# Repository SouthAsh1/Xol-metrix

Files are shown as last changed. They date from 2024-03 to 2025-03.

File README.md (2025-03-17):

# Xol-metrix

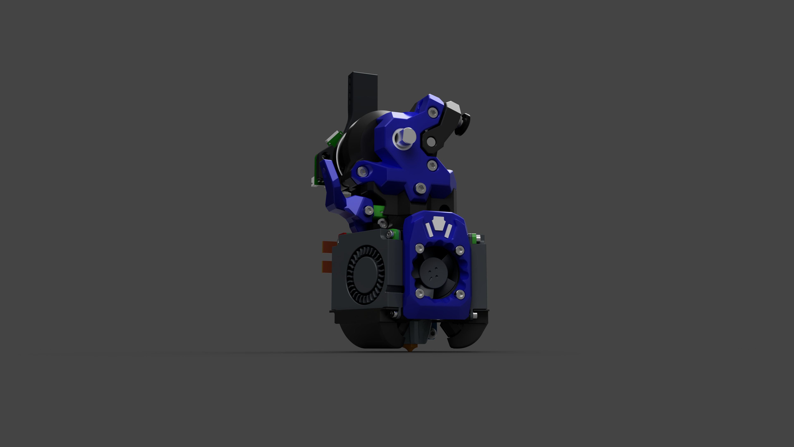
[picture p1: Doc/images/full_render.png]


This is a filament cutter designed around the Xol Toolhead platform thanks to everyone that helped with the BETA process to get this project into a phase that I am comfortable in calling a released state. There will still be some small adjustments I will make when more feedback is given.

Now supports current version of Xol Toolhead! CAD included.

Does support non-heatset version of Xol, however, the cutting arm mount still requires it. So anything that is non-heatset does not require heatsets asside from that.

I do ask that if anyone makes any mods let me know so we can discuss if it makes since to put it in the repo.

So far the project supports the following.

### Hotends

- Dragon SF/UHF/ACE
- NF-Crazy
- Rapido SF/UHF
- Rapido V2 SF/UHF
- Revo Voron
- DropEffect XG
- Bambu Labs

### Extruders

- [Wrist Watch G2](https://github.com/tetsu97/WristWatch-G2-Extruder)
- [Sherpa Mini](https://github.com/Annex-Engineering/Sherpa_Mini-Extruder)
- [Orbiter](https://www.orbiterprojects.com/orbiter-v2-0/)
- [G2SA](https://github.com/tetsu97/Galileo2)
- [VZ Hextrudort](https://github.com/VzBoT3D/Vz-HextrudORT) / [Bondtech LGX Lite](https://www.bondtech.se/product/lgx-lite-v2-large-gears-extruder/)
## BOM

This is addition to your choice of Xol Toolhead build BOM

|Qty|Item|Notes|
|-|-|-|
|2|M2 Flanged Heatset Insert|Specifically this heatset [HM20X157C](https://www.digikey.com/en/products/detail/tri-star-industries-inc/HM20X157C/14205393)|
|1|M2.5 Heatset Insert|3.5mm Outer Diameter x 4mm Length `Same as Xol Toolhead BOM`|
|3|M2 Heatset Insert|3.5mm Outer Diameter x 4mm Length `Same as Xol Toolhead BOM`|
|2|M2.5x15 SHCS|For mounting the arm to the frame and blade holder.|
|3|M2x8 SHCS|To hold the extruder adapter together.|
|1|5.5mm Ball Bearing|For toolhead filament sensor. `Same as ERCF BOM`|
|1|Omron D2F Micro Switch|Tis be switch that does clicky things.|
|2|M2x10 Self Tapping|It really doesn't matter what type just has to self tap.|
|1|0.5x4x15 Spring|Any spring that is 4mm in diameter and no longer than 15mm should work your milage may vary for cutting force needed.|
|Yes|PTFE Tube|Still working out exact lengths and possibly cutting jigs.|
|**OPTIONS**|
|1|#4 metal hobby blades|Same blade used in the Filametrix only cut to a different length.|
|**OR**|
|1|OLFA KB4-F/5|Different blade otion if you are having problems with #4 blades.|
|**OPTIONAL**|
|1|M3 Grubscrew|Same ones used to secure pulleys **totally optional**.|

## Acknowledgements

 - [Xol-Toolhead](https://github.com/Armchair-Heavy-Industries/Xol-Toolhead) For Xol Toolhead project
 - [WristWatch-G2-Extruder](https://github.com/tetsu97/WristWatch-G2-Extruder) For WWG2 and Extruder adapter
 - [Filametrix](https://github.com/sorted01/Filametrix) For the orginal mod idea
 - Thanks to Tea/`nurse.shark` for alowing me to use the Xolametrix name (I did change it slightly)
 - Thanks to scheini79/`zerodegree79` for the XolPAP modification.

## Feedback

- [Armchair Discord User Projects Discussion](https://discord.com/channels/1029426383614648421/1195580104659710053)
- My Discord `southash1`

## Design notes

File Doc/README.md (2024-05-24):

# Xol-metrix Assembly

This project assumes you know how to build the standard Xol Toolhead with this build assembly thrown into the mix.

|	Notes	|	Image	|
|	---	|	---	|
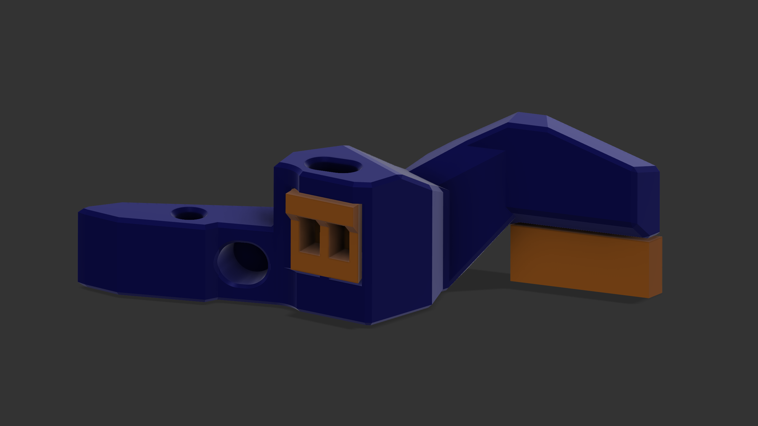
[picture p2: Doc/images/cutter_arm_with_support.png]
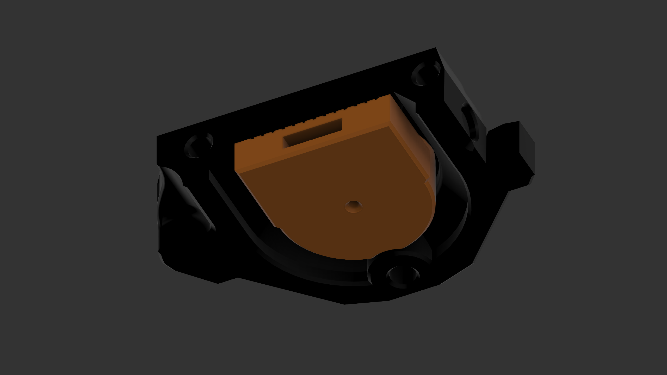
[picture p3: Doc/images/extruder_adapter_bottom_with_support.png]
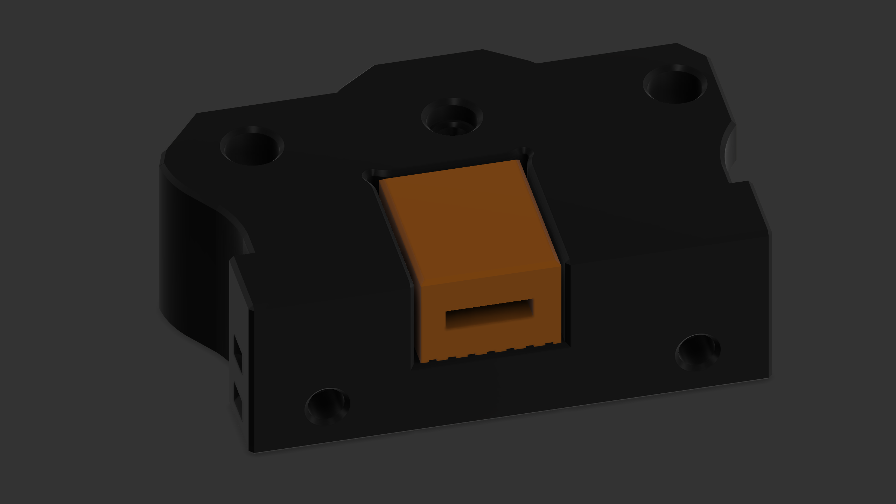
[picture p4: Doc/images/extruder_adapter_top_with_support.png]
|Remove the support material in orange. They should break away with ease.|	|
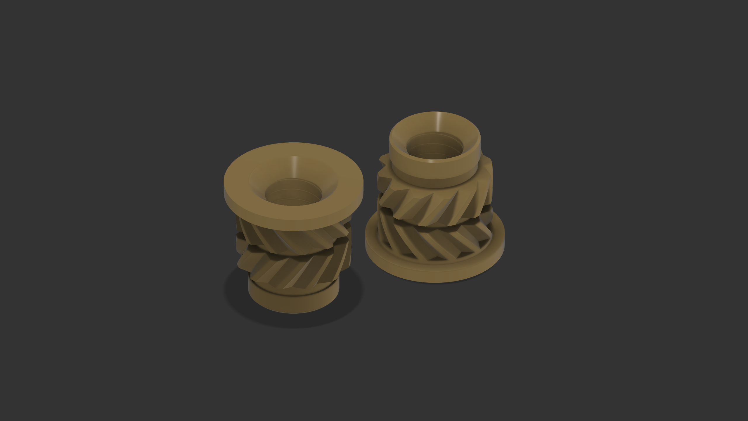
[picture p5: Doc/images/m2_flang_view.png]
|Next drill out the 2 `Flanged M2` Heatset Inserts with a `5/64 inch drill bit`. Then use the `#2 center drill bit` to chamfer the top of one and the bottom of the other. ⚠⚠ **Make sure you thuroghly clean the inserts of brass when done!** ⚠⚠||
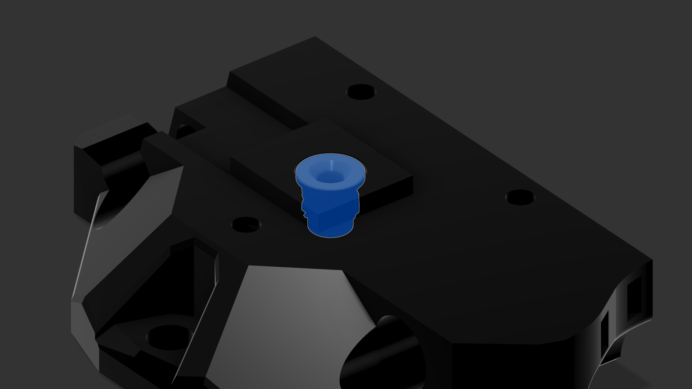
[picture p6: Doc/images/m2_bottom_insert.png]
|Insert the `Flanged M2` heatset with the **top chamfer** into the `extruder_adapter_bottom.stl` with the flang surface flush with the printed surface.||
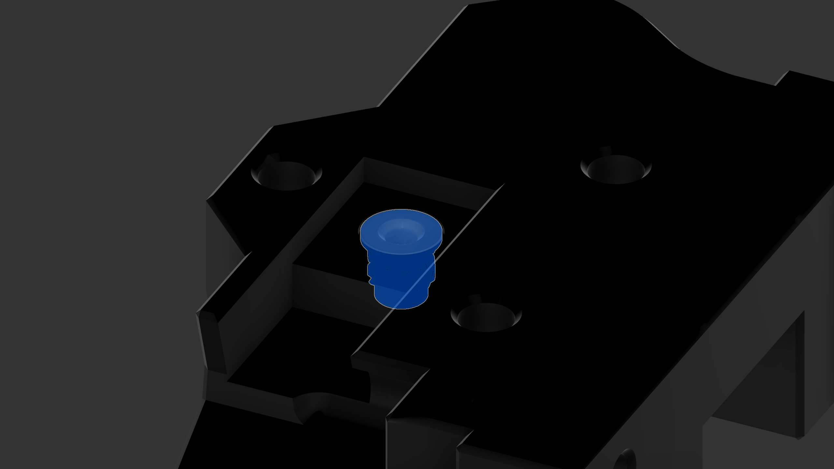
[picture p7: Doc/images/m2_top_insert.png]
|Insert the `Flanged M2` heatset with the **bottom chamfer** into the `extruder_adapter_top_(your_choice_here).stl` with the flang surface flush with the printed surface.||
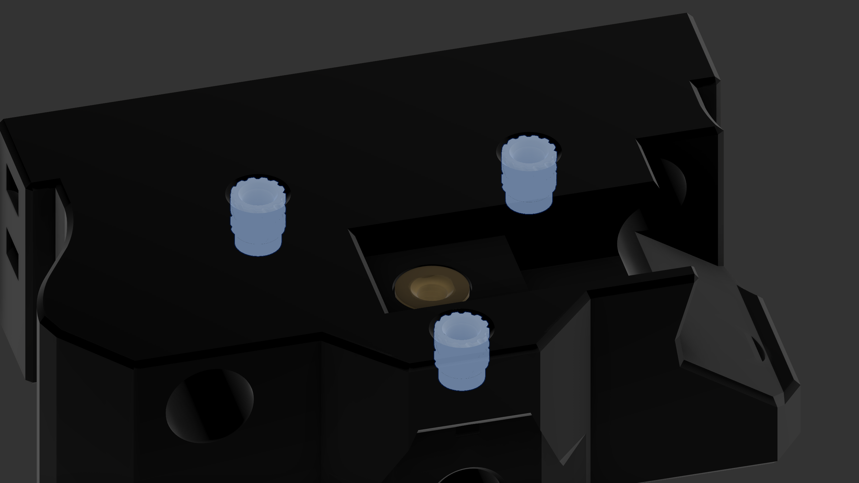
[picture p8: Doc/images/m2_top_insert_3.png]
|Next insert the 3 `M2x3.5x4 Heatsets` into the 3 holes in the `extruder_adapter_top_(your_choice_here).stl`.||
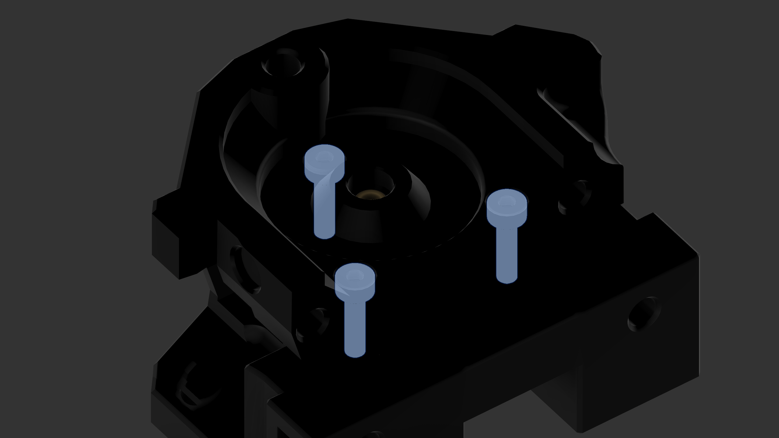
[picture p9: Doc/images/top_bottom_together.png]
|Screw the `extruder_adapter_top_(your_choice_here).stl` and `extruder_adapter_bottom.stl` together with `M2x8 SHCS` ⚠Do not over tighten!⚠ ||
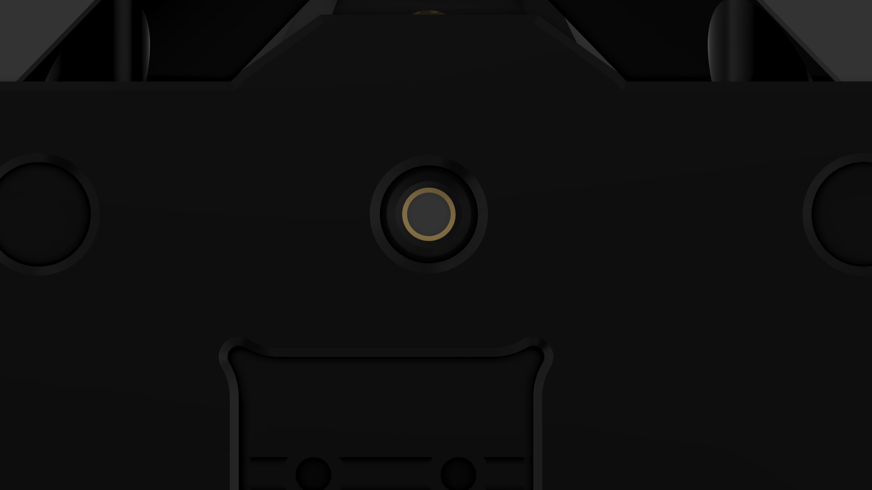
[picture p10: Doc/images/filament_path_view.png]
|Clean the inside of the filament path with a `5/64 inch drill bit` it may have some ooze from istalling the Heatset inserts.||
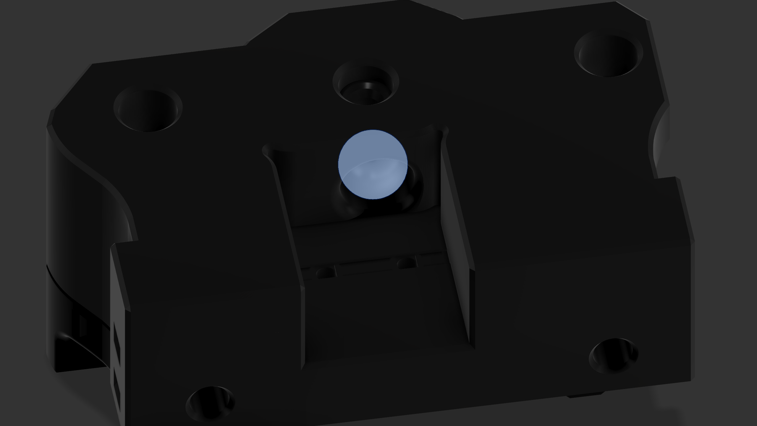
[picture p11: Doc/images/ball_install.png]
|Place the `5.5mm Ball Bearing` in the hole on top of the extruder adapter.||
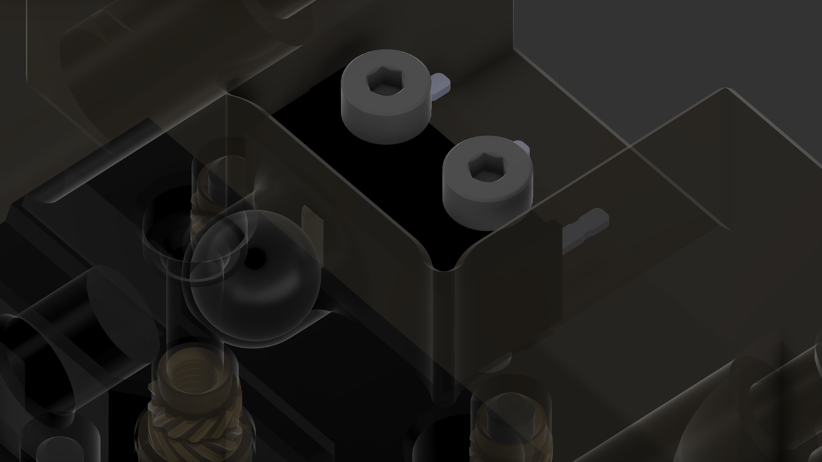
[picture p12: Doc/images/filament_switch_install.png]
|Put the `Omron D2F` (with no lever) into slot with clicker behind the Ball Bearing, secure with `M2x10 Self Tapping Screws`.||
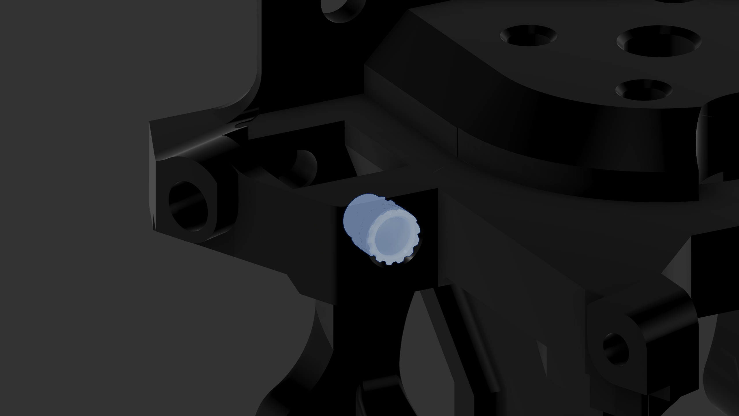
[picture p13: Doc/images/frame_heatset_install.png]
|Insert one `M2.5x3.5x4 Heatset` into the hotend mount (rest of hotend heatsets are not explained refer to Xol 2 Docs).||
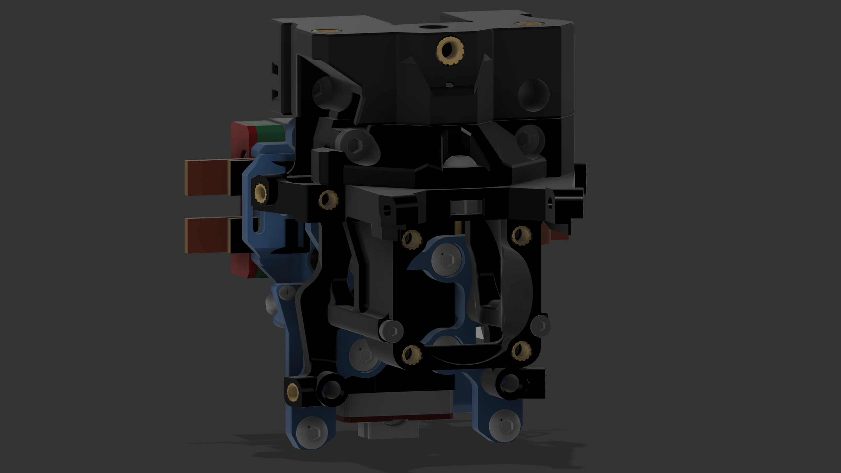
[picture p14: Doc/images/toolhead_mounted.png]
|Install extruder adapter onto the `HE Mount` of your choice and install on your carriage of choice. (Tap option shown in picture)||
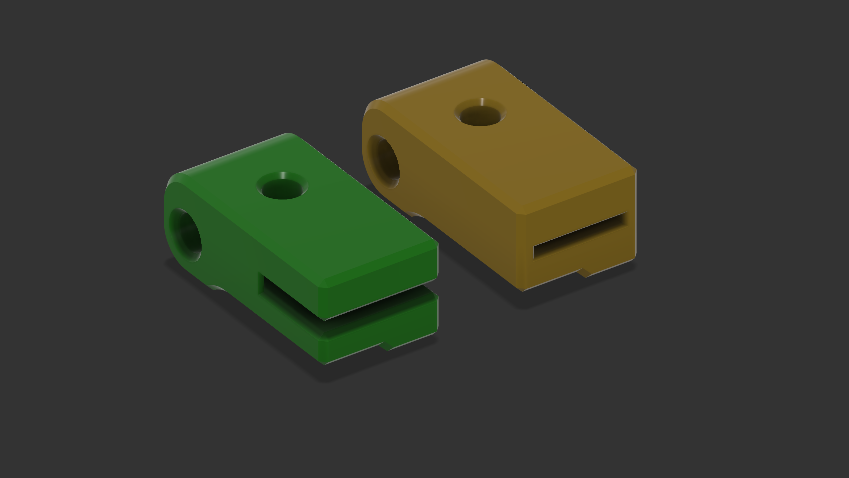
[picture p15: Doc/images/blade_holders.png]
|Select the Blades of your choice `#4` (Yellow) or `OLFA KB4-F/5` (Green).||
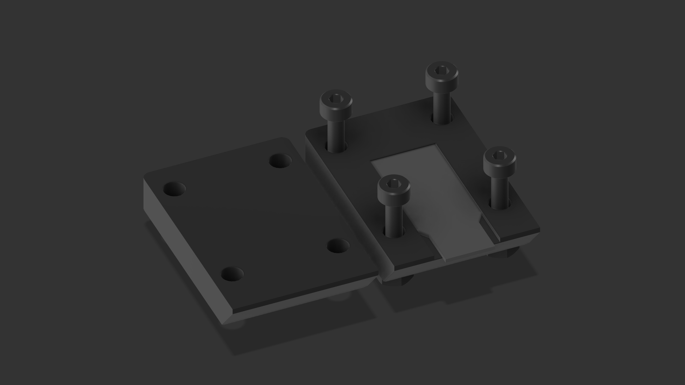
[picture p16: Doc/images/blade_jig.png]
|Use the Blade Jig that coresponds with your blade of choice #4 / OLFA and clamp the blade in it with the blade sticking in. **Final length should be ~20mm.**||
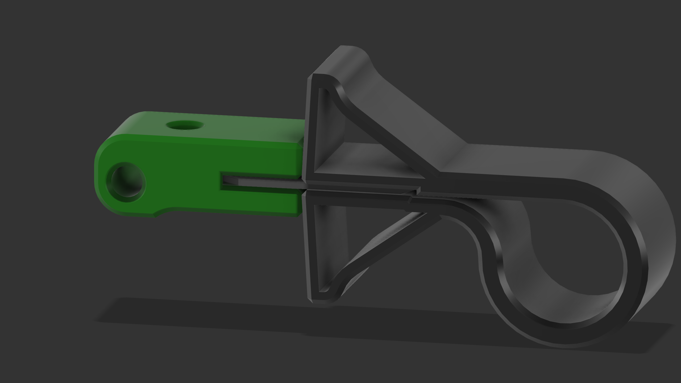
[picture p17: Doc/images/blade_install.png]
|Use the `blade_install_tool.stl` to install the blade. ⚠⚠ **Take extra precaution as the blades do not care and will go through your skin with no remorse and then the red sauce comes out!** ⚠⚠||
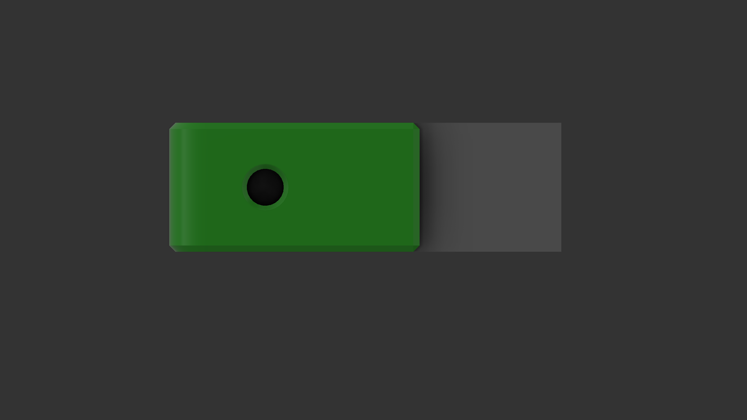
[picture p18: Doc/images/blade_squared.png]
|Insure that the blade is squared up with the `[b]_blade_holder_(your_choice_here).stl`. The hole on top is big enough for an `M3 Grub Screw` or you can glue the blade in.||
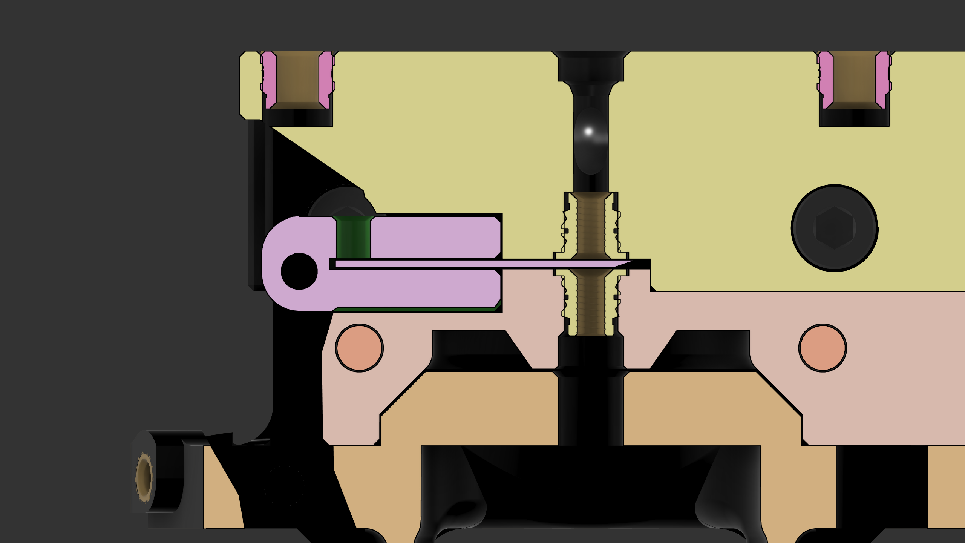
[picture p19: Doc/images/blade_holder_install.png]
|Slide the Blade Holder into the Extruder adapter carefully aligning the blade into the slot.||
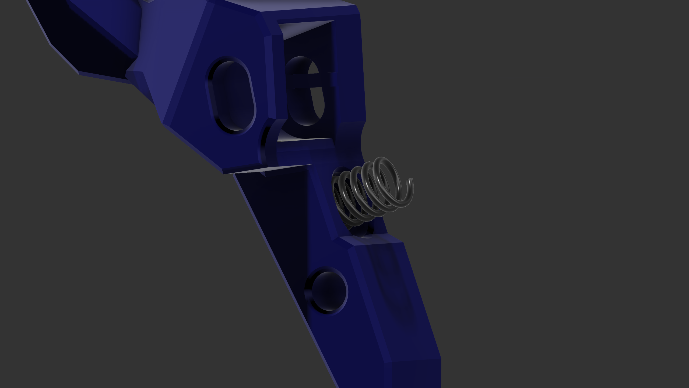
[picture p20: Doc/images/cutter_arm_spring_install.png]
|Install the Spring into the slot on the `[a]_cutter_arm.stl`.||
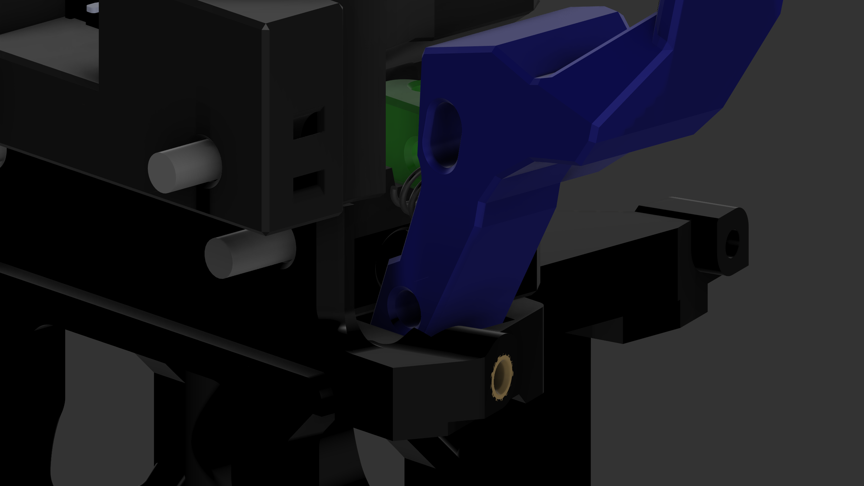
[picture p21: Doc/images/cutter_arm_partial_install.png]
|Slide the cutter arm into the slot on the Hotend Frame partially **Do not kink the spring**.||
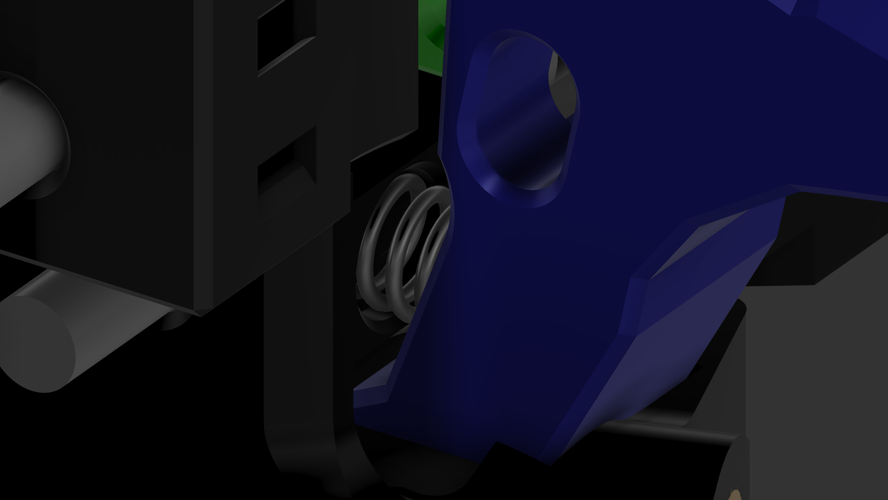
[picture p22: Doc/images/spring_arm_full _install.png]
|Use a small slim screwdriver of sorts to persuade the spring into the recess in the extruder mount while sliding the arm into its final position.||
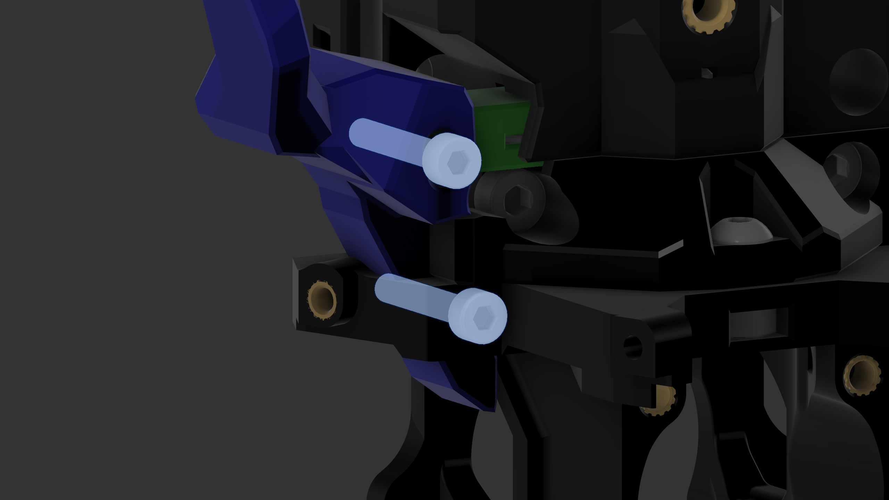
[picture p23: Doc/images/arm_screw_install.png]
|Install the 2 `M2.5x15 SHCS` into the frame and blade holder to finish up the cutter install.||
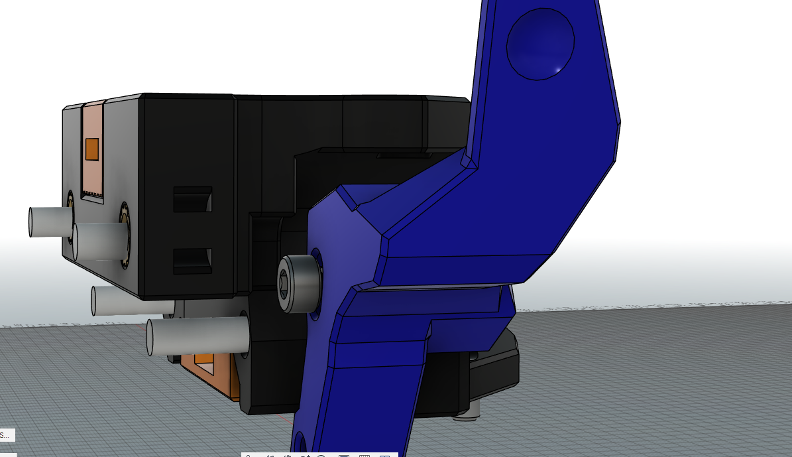
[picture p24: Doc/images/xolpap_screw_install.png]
|If using XolPAP Install the `M2.5x15 SHCS` on the back side of the arm shown here. (Thanks to scheini79 for the suggestion!)||
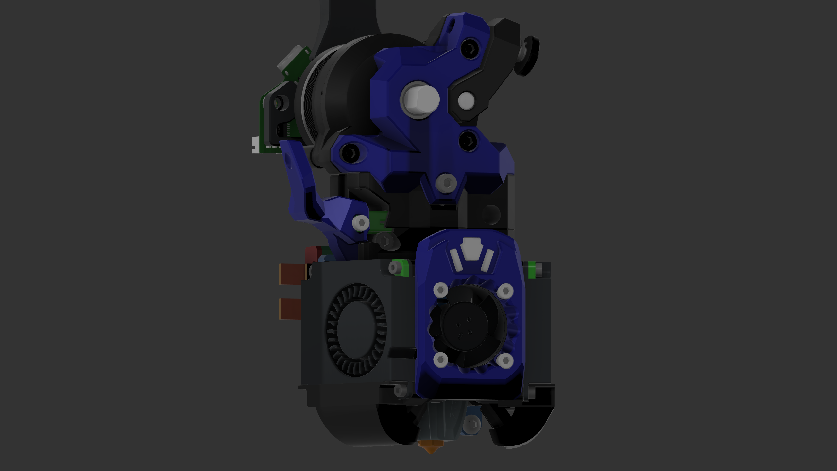
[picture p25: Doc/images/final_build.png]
|After all this the rest of the Xol Toolhead will go together the same as the standard one.||

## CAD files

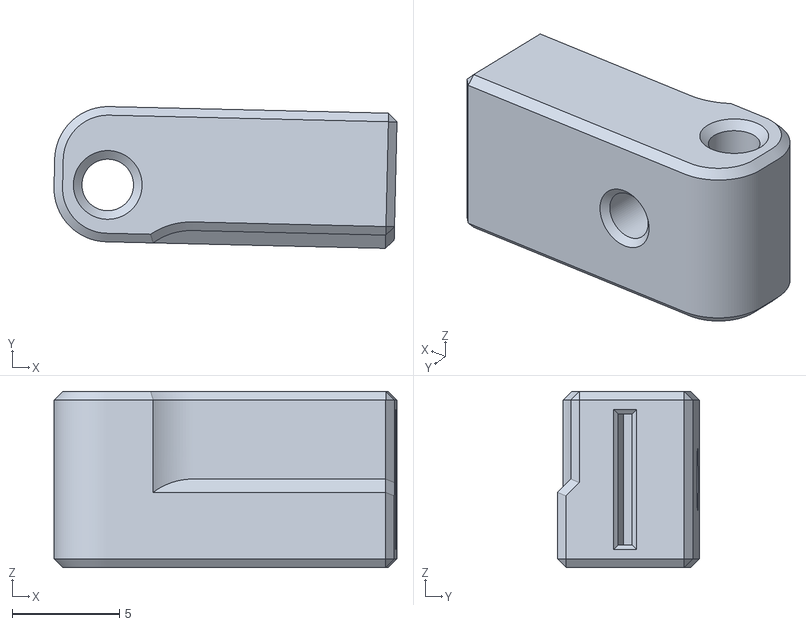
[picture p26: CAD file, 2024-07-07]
STL/[b]_blade_holder_4.stl
16.0 x 6.60 x 8.20

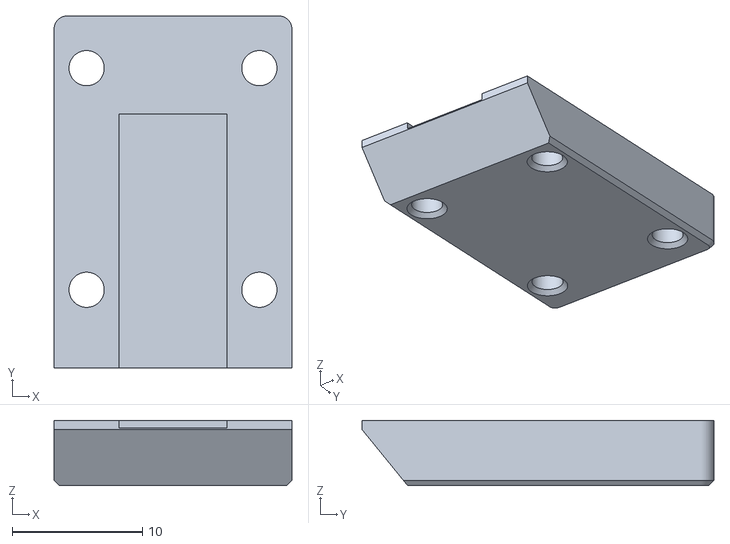
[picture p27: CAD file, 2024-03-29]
STL/Blade Tools/blade_snap_jig_OLFA_bottom.stl
18.2 x 27.0 x 5.00

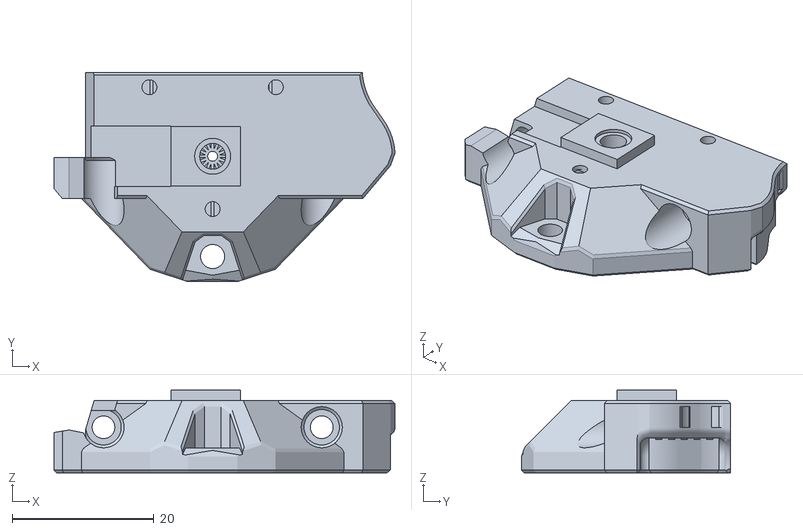
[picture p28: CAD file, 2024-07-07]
STL/Extruder Mounts/extruder_adapter_bottom.stl
48.1 x 29.6 x 11.7

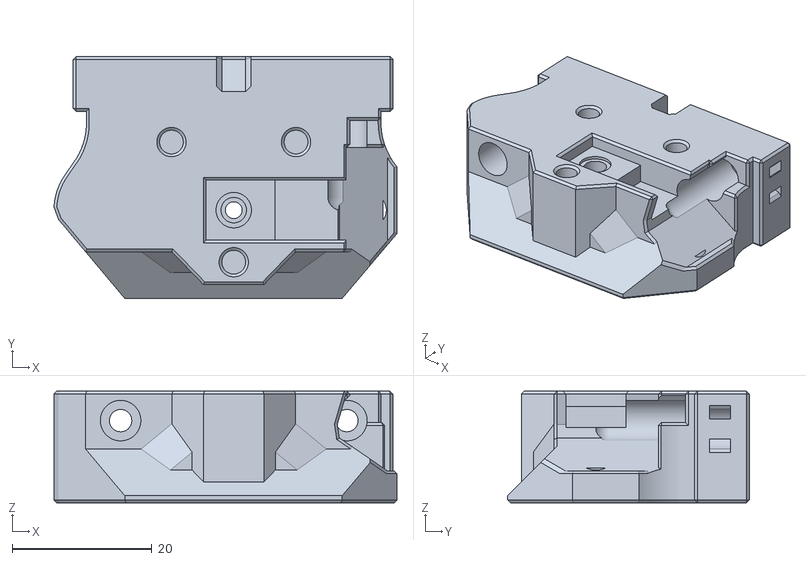
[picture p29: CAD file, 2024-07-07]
STL/Extruder Mounts/TAP Carriage/HeatSet/extruder_adapter_top_Orbiter.stl
49.1 x 34.6 x 16.0

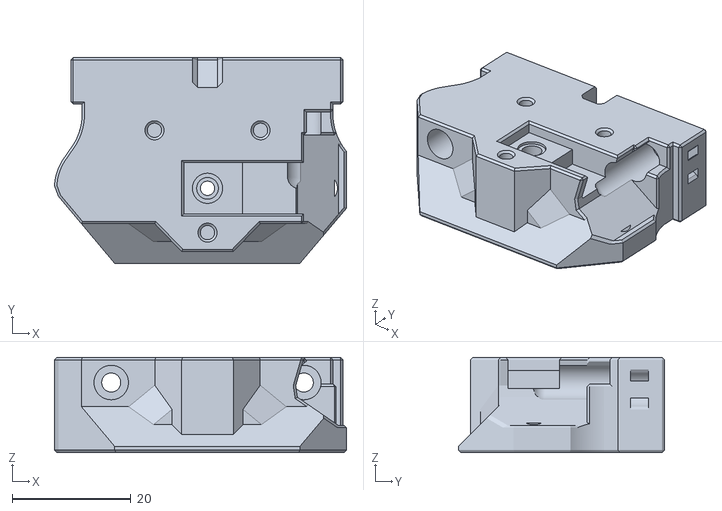
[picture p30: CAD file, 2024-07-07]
STL/Extruder Mounts/TAP Carriage/Non-HeatSet/extruder_adapter_top_Orbiter.stl
49.1 x 34.6 x 16.0

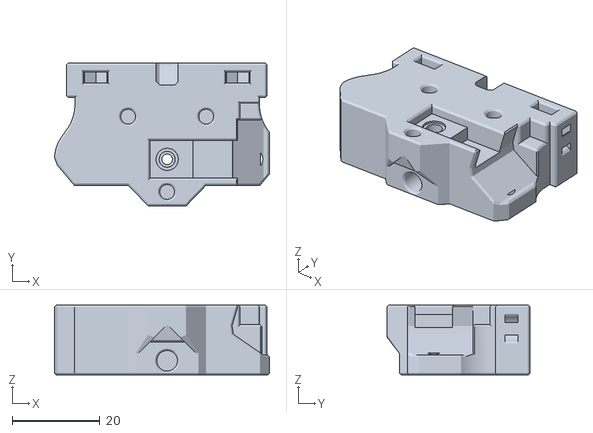
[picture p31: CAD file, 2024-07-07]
STL/Extruder Mounts/XOL Carriage/HeatSet/extruder_adapter_top_G2SA.stl
49.1 x 32.6 x 16.0

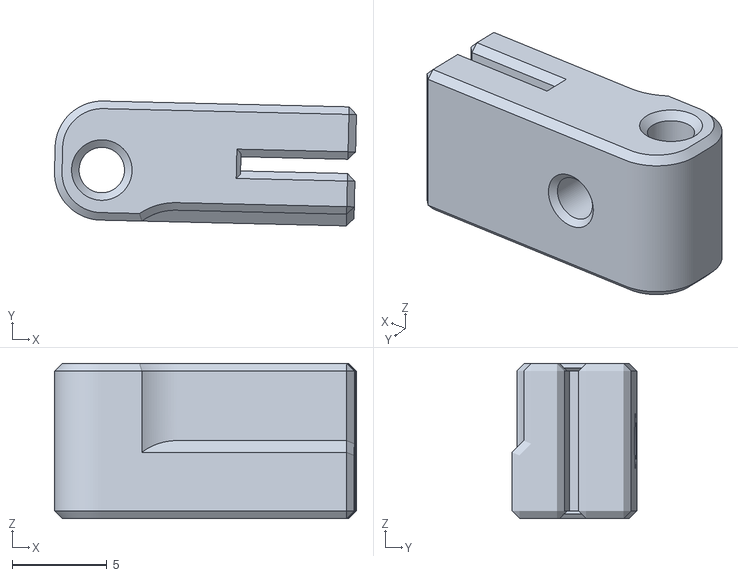
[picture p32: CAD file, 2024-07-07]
STL/[b]_blade_holder__olfa.stl
16.0 x 6.60 x 8.20

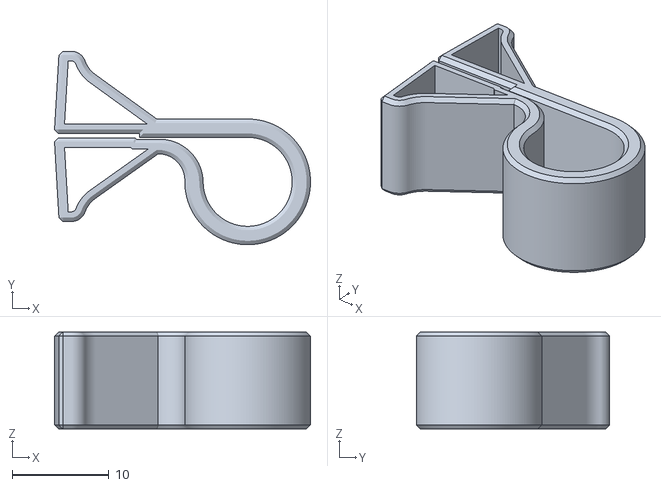
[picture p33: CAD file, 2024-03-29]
STL/Blade Tools/blade_install_tool.stl
26.5 x 20.0 x 10.0

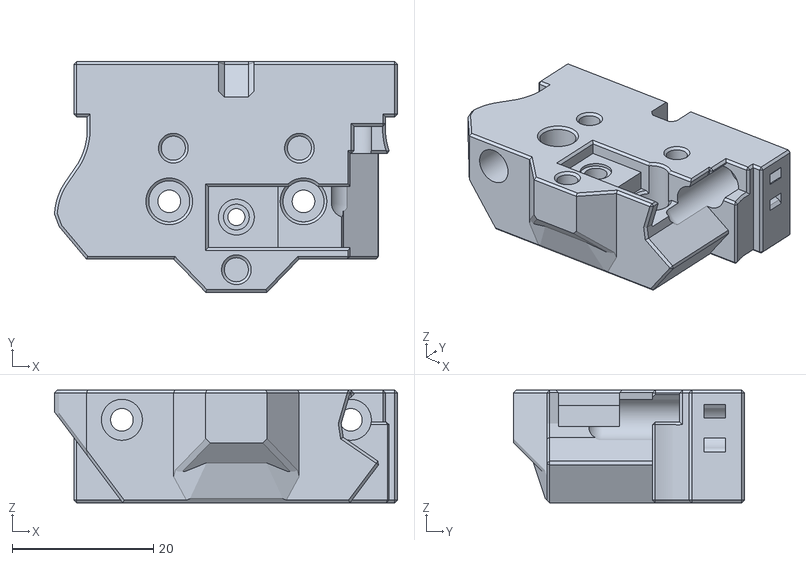
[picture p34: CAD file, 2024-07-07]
STL/Extruder Mounts/TAP Carriage/HeatSet/extruder_adapter_top_VZ-Hex+LGX-L.stl
48.5 x 32.6 x 16.0

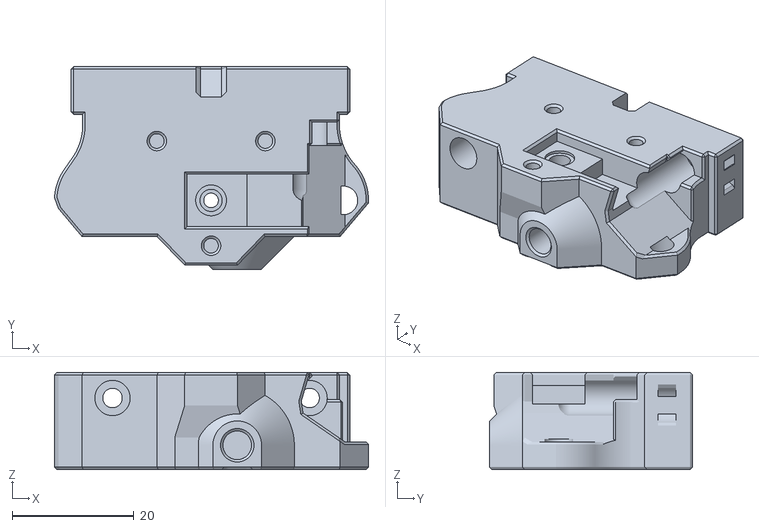
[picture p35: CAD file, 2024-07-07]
STL/Extruder Mounts/TAP Carriage/Non-HeatSet/extruder_adapter_top_Sherpa_Mini.stl
51.6 x 33.3 x 16.0

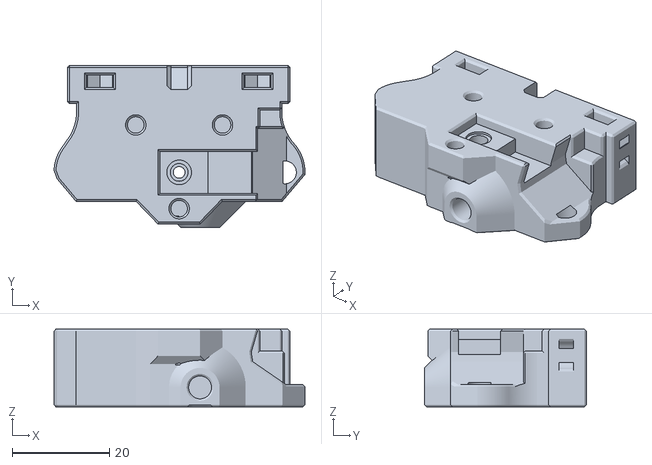
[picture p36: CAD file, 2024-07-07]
STL/Extruder Mounts/XOL Carriage/HeatSet/extruder_adapter_top_Sherpa_Mini.stl
51.6 x 33.3 x 16.0

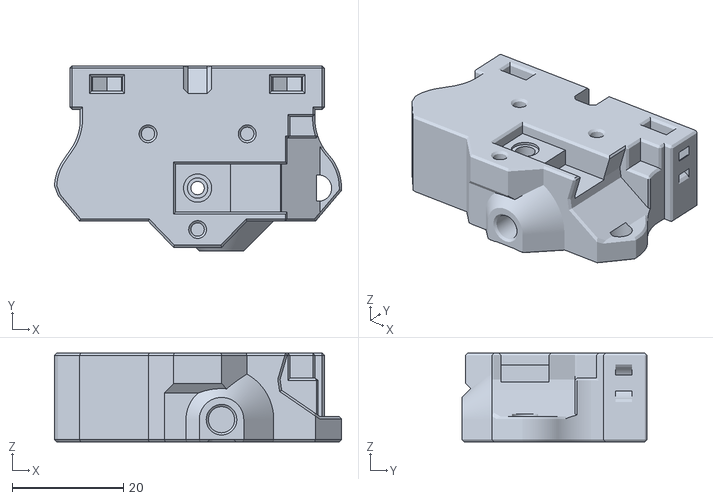
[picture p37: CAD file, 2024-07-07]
STL/Extruder Mounts/XOL Carriage/Non-HeatSet/extruder_adapter_top_Sherpa_Mini.stl
51.6 x 33.3 x 16.0

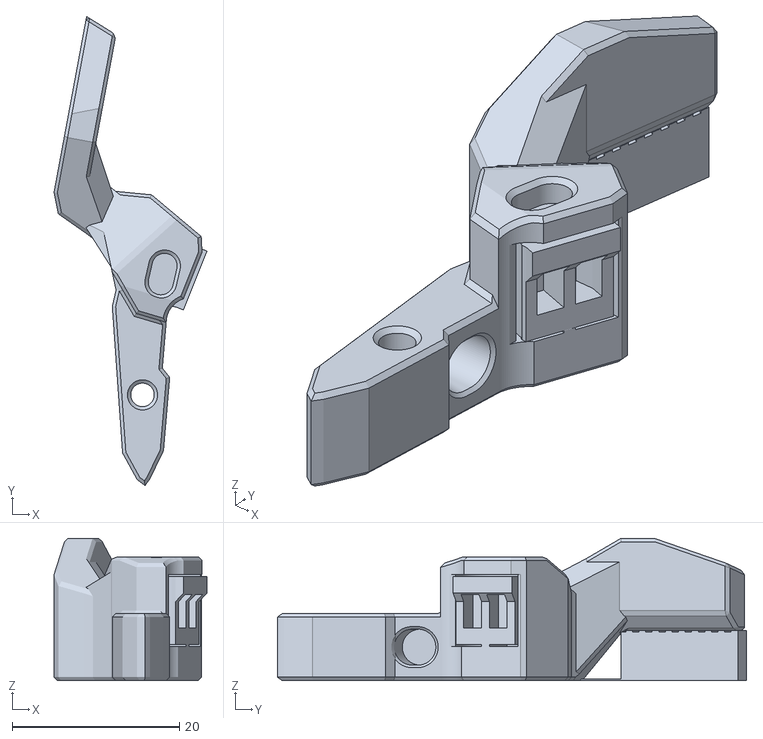
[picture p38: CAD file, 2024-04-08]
STL/[a]_cutter_arm.stl
18.3 x 56.0 x 17.0

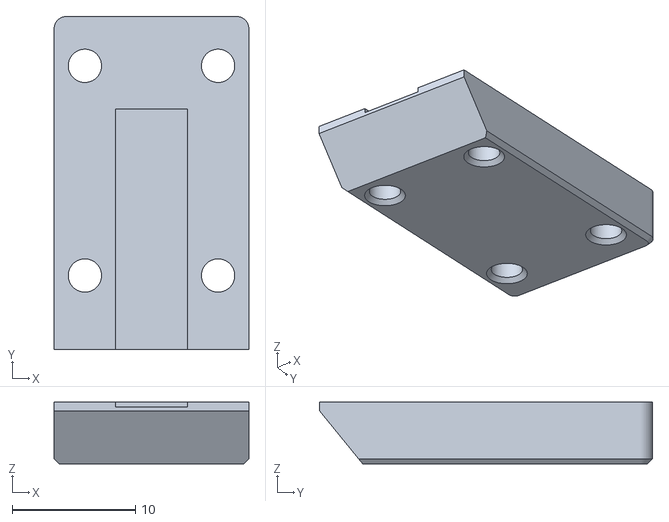
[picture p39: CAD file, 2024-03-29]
STL/Blade Tools/blade_snap_jig_4_bottom.stl
15.8 x 27.0 x 5.00

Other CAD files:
STL/Extruder Mounts/XOL Carriage/Non-HeatSet/extruder_adapter_top_WWG2.stl
STL/Extruder Mounts/TAP Carriage/HeatSet/extruder_adapter_top_WWG2.stl
STL/Extruder Mounts/TAP Carriage/Non-HeatSet/extruder_adapter_top_WWG2.stl
STL/Extruder Mounts/XOL Carriage/HeatSet/extruder_adapter_top_WWG2.stl
STL/Blade Tools/blade_snap_jig_4_top.stl
STL/Blade Tools/blade_snap_jig_OLFA_top.stl
STL/Extruder Mounts/TAP Carriage/HeatSet/extruder_adapter_top_G2SA.stl
STL/Extruder Mounts/TAP Carriage/HeatSet/extruder_adapter_top_Sherpa_Mini.stl
STL/Extruder Mounts/TAP Carriage/Non-HeatSet/extruder_adapter_top_G2SA.stl
STL/Extruder Mounts/TAP Carriage/Non-HeatSet/extruder_adapter_top_VZ-Hex+LGX-L.stl
STL/Extruder Mounts/XOL Carriage/HeatSet/extruder_adapter_top_Orbiter.stl
STL/Extruder Mounts/XOL Carriage/HeatSet/extruder_adapter_top_VZ-Hex+LGX-L.stl
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

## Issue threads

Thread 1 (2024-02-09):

Part orientation

oldcrazyeye, 2024-02-09:
Not really an issue but a suggestion. I know orientating parts in fusion sucks but you can orientate them in super slicer then export as stl. Disregard if you already know this

SouthAsh1, 2024-02-09:
Yea I have a message in the STL folder, my fusion 360 is not wanting to export the models in the orientation I put them in. I'll look into it soon.

Closed 2024-02-09.

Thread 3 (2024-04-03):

Trouble printing cutter arm

D20180, 2024-04-03:
V0.2 esun ABS+ Orcaslicer no Z-hop

Having problems printing, the built in support won't stay on the one strip supporting it, curls up and gets knocked off.

SouthAsh1, 2024-04-04:
So not saying that I can't modify the model to make it slightly easier to print but how high are your fans?
I also believe that Esun ABS+ is not the friendlest at printing and likes to warp on installed parts based on the voron discord.

However I will take a look this weekend as got a few minor updates to work on :)

SouthAsh1, 2024-04-14:
Closing issue as I have modified the model to make it easier to print and D20180 has not commented any further.

Closed 2024-04-14.

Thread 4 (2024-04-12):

Ball bearing is not standard BOM?

LandonPatmore, 2024-04-12:
I have an ERCF and looked through my kit contents that came from https://dfh.fm/products/enraged-rabbit-carrot-feeder?_pos=6&_sid=a5b37ae28&_ss=r and also the official BOM here https://docs.google.com/spreadsheets/d/1A_qeNeaVprh_iPbvLcLjvJ2o2NfCzjuJam3K3RkWW0w/edit#gid=0 and there does not seem to be a mention of a ball bearing anywhere there?

SouthAsh1, 2024-04-12:
It is a 5.5mm ball bearing that is standard on the ERCF v2 BOM for the ERCT buffer system I will update the repo to clarify sorry about that!

LandonPatmore, 2024-04-12:
Ah looks like I have an ERCG v1 build, whoops!

SouthAsh1, 2024-04-12:
All good!

Closed 2024-04-12.

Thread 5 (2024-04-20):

What xolpap duct fits xol metrix?

GTreaper, 2024-04-20:
which version of the xolpap duct fits this HE mount? anybody know?

Thanks

GTreaper, 2024-04-22:
Found the right one after some different prints.

Closed 2024-04-22.

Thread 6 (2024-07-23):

No issue just a question

GTreaper, 2024-07-23:
Is everything updated to match the latest revision of the XOL?

DianosOdd, 2024-07-26:
I would love as well

SouthAsh1, 2024-07-26:
Sorry just saw this, yes the STLs are updated I just haven't updated the CAD and README files yet.
There is everything for Heatset and non-Heatset versions.
I will try to get some of it updated this weekend.

Closed 2024-07-26.

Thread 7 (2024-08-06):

Question

bobwarsrvng, 2024-08-06:
Step #2:
Next drill out the 2 Flanged M2 Heatset Inserts with a 5/64 inch drill bit. Then use the #2 center drill bit to chamfer the top of one and the bottom of the other. ⚠⚠ Make sure you thuroghly clean the inserts of brass when done! ⚠⚠

I have a couple of questions:

1. What if I can't get the [HM20X157C] listed in the BOM? Digikey and Mouser are both on backorder and everyone else seems to want multiple thousands to process an order. I only need a couple.

1.a Would this work? Comes pre-chamfered

https://www.amazon.com/gp/product/B088QJG676/ref=ewc_pr_img_1?smid=A2L1PKBL5IWW8M&psc=1

3. I'm trying to understand the purpose of the chamfer here. If I am understanding, I would drill out the threads to make a nice smooth passage for filament and then countersinking the top / bottom to allow for the filament to have a small margin of error when inserting. Like a funnel.

and a bonus,

⚠⚠ Make sure you **<spelling>thuroghly</spelling>** clean the inserts of brass when done! ⚠⚠

Also, I feel I must explain myself for doing this as an issue. The discord link won't let a non-student like me to access the link (Its been more than a few years) and I couldn't find your username in Discord. I might just be old though.

Otherwise, this is an amazing project!

I hope it ends up being mainlined!

SouthAsh1, 2024-08-07:
So I'm looking at an alternative for the heatset just haven't decided what I'm wanting to go with yet. That heatset is too small, there is barely anything there after drilling it out. Last yes the chamfer is for small margins of error when the filament is re-inserted. Though my design is a lot tighter than others, it's better to have than not.

Idk about the discord link thing as it should work as long as you are in the Armchair discord.

Closed 2024-08-13.

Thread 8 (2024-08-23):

BambuLab Supports do not line up with hotend mount

StacyLow, 2024-08-23:
The bambulab supports only line up with the hotend mount for the BambuLab Fan Heatset model (which looks to be the long version). I have fixed this and will raise a PR

SouthAsh1, 2024-08-23:
Hahaha oops I _really_ messed those up! They are fixed now, I'll try to get the CAD updated at some point.

StacyLow, 2024-08-23:
Oh that was quick! I've made a branch with the updated CAD, do you want me to publish it?

SouthAsh1, 2024-08-23:
No it's ok I already have it I just have to re-upload it, and I think I might restructure the CAD files to how Taz has the official Repo

Closed 2024-08-23.

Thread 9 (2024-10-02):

Extruder/toolhead parameters for HappyHare

pbutler, 2024-10-02:
This is as much a question as a suggestion but I can't add labels:

I might have missed it but does anyone have any dimensions/parameters for using this mod with Happy Hare.  I realize that these are dependent on the hotend/extruder choices but a wiki page where we could share parameters or other documentation could be helpful.  I know these can probably be measured in Fusion but I am not particularly adept at Fusion.

In particular the parameters below are what I am talking about.  There might be others but I took poor notes when I was setting this all up.  These shouldn't be held up as an example.  My tuning parameters are quite large and this was all hand tuned until I gave up and things mostly (but not always work):

In `mmu_parameters.cfg` (for a Rapido 2 SF and Orbiter 2).
```yaml
# Toolhead loading and unloading --------------------------------------------------------------------------------------
# ████████╗ ██████╗  ██████╗ ██╗     ██╗  ██╗███████╗ █████╗ ██████╗     ██╗      ██████╗  █████╗ ██████╗
# ╚══██╔══╝██╔═══██╗██╔═══██╗██║     ██║  ██║██╔════╝██╔══██╗██╔══██╗    ██║     ██╔═══██╗██╔══██╗██╔══██╗
#    ██║   ██║   ██║██║   ██║██║     ███████║█████╗  ███████║██║  ██║    ██║     ██║   ██║███████║██║  ██║
#    ██║   ██║   ██║██║   ██║██║     ██╔══██║██╔══╝  ██╔══██║██║  ██║    ██║     ██║   ██║██╔══██║██║  ██║
#    ██║   ╚██████╔╝╚██████╔╝███████╗██║  ██║███████╗██║  ██║██████╔╝    ███████╗╚██████╔╝██║  ██║██████╔╝
#    ╚═╝    ╚═════╝  ╚═════╝ ╚══════╝╚═╝  ╚═╝╚══════╝╚═╝  ╚═╝╚═════╝     ╚══════╝ ╚═════╝ ╚═╝  ╚═╝╚═════╝
#
# It is possible to define highly customized loading and unloading sequences, however, unless you have a specialized
# setup it is probably easier to opt for the built-in toolhead loading and unloading sequence which already offers a
# high degree of customization. If you need even more control then edit the _MMU_LOAD_SEQUENCE and _MMU_UNLOAD_SEQUENCE
# macros in mmu_sequence.cfg - but be careful!
#
# An MMU must have a known point at the end of the bowden from which it can precisely load the extruder. Generally this
# will either be the extruder extrance (which is controlled with settings above) or by homing to toolhead sensor. If
# you have toolhead sensor it is past the extruder gear and the driver needs to know the max distance (from end of
# bowden move) to attempt homing
#
toolhead_homing_max: 55			# Maximum distance to advance in order to attempt to home to defined homing endstop

# IMPORTANT: These next three settings are based on the physical dimensions of your toolhead
# Once a homing position is determined, Happy Hare needs to know the final move distance to the nozzle. There is only
# one correct value for your setup - use 'toolhead_ooze_reduction' (which corresponds to the residual filament left in
# your nozzle) to control excessive oozing on load. See doc for table of proposed values for common configurations.
#
# NOTE: If you have a toolhead sensor you can automate the calculation of these parameters! Read about the
# `MMU_CALIBRATE_TOOLHEAD` command (https://github.com/moggieuk/Happy-Hare/wiki/Blobing-and-Stringing)
#
toolhead_extruder_to_nozzle: 84		# Distance from extruder gears (entrance) to nozzle
toolhead_sensor_to_nozzle: 62		# Distance from toolhead sensor to nozzle (ignored if not fitted)
toolhead_entry_to_extruder: 8		# Distance from extruder "entry" sensor to extruder gears (ignored if not fitted)

# TUNING: The is a tuning setting that represents how much residual filament is left behind in the nozzle when filament
# is removed, it is thus used to reduce the extruder loading length and prevent excessive ooze.
# It is important to tune this parameter and not the dimensions above which are shared by other logic. If using a wipetower
# and you experience blobs on it, increase this value (reduce the quantity of filament loaded). If you experience gaps,
# decrease this value. If gaps and already at 0 then perhaps the 'toolhead_extruder_to_nozzle' setting is incorrect.
# Also see 'retract' setting in 'mmu_macro_vars.cfg' for final in-print blob tuning.
#
# NOTE: If you have a toolhead sensor you can automate the calculation of this parameter! Read about the
# `MMU_CALIBRATE_TOOLHEAD` command (https://github.com/moggieuk/Happy-Hare/wiki/Blobing-and-Stringing)
#
toolhead_ooze_reduction: 5		# Reduction in extruder loading length to fine tune ooze (default: 0mm)

# Distance added to the extruder unload movement to ensure filament is free of extruder. This adds some degree of tolerance
# to slightly incorrect configuration or extruder slippage. However don't use as an excuse for incorrect toolhead settings
#
toolhead_unload_safety_margin: 20	# Extra movement saftey margin (default: 10mm)
```

and in `mmu_macro_vars.cfg`:
```yaml
# Distance from the internal nozzle tip to the cutting blade. This dimension
# is based on your toolhead and should not be used for tuning
# Note: If you have a toolhead sensor this variable can be automatically determined!
# Read https://github.com/moggieuk/Happy-Hare/wiki/Blobing-and-Stringing
variable_blade_pos              : 51		; TUNE ME: Distance in mm from internal nozzle tip

# Distance to retract prior to making the cut, measured from the internal nozzle
# tip. This reduces wasted filament (left behind in extruder) but might cause a
# clog if set too large. This must be less than 'blade_pos'
# Note: the residual filament left in nozzle ('toolhead_ooze_reduction') is
# subtracted from this value so make sure toolhead is calibrated
variable_retract_length         : 35		; TUNE ME: 5mm less than 'blade_pos' is a good starting point
```

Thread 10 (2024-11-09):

Non-heatset extruder mount models in heatset folder?

warpedscale, 2024-11-09:
Hello,

I noticed in this folder: STL/Extruder Mounts/XOL Carriage/HeatSet/ every model had places for M3 nuts in the back of the extruder mounts that mounts to the carriage instead of heatset inserts. Is that supposed to be the case?

SouthAsh1, 2025-04-10:
Yes, as this is how normal XOL works.

Closed 2025-04-10.

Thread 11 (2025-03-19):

M2 / 2.5 Heat set

cyph3r42, 2025-03-19:
BOM references M2 and M2.5 heat sets that are on the Xol BOM.  Current Xol BOM only lists M3 heat set inserts.

Is there a plan to move to M3?

cyph3r42, 2025-03-19:
After reviewing the cad, I'm not sure there's room to possibly move to M3.

cyph3r42, 2025-03-20:
Got it.  So the direction is to go to screwing into plastic primarily.  Just trying to make sure I ultimately have the right hardware.

Closed 2025-03-19.

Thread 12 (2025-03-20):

BOM and Documentation refers to M2.5 x 15 SHCS but CAD differs

EvilGoldfish, 2025-03-20:
The BOM and assembly documents refer to M2.5 x 15 SHCS. The CAD shows M2.5 x 16 SHCS.
I noticed this because I can't find any source of M2.5 x 15 and didn't want to have to bother grinding anything down.

SouthAsh1, 2025-04-10:
apologies for not responding sooner but 16mm length will work it looks like I was typing the wrong thing the entire time lol, I'll fix it soon as I need to go over this project again anyways to clean it up a bit more.

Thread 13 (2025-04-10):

printing the cutting arm with a 0.2 layer height causes the support inside the cutout to fuse to the bottom

Nathan22211, 2025-04-10:
doing it at 0.15 doesn't seem to help too much either despite the preview showing otherwise, orca slicer 2.3

SouthAsh1, 2025-04-10:
do you have a .25 first layer?

Nathan22211, 2025-04-10:
No and I guess I didn't see that

Get Outlook for Android<https://aka.ms/AAb9ysg>
________________________________
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

SouthAsh1, 2025-04-10:
All good I don't have the print settings on the Docs, whenever I get the chance to clean everything up I'll add it!

Closed 2025-04-10.

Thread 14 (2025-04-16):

Toggling Toolhead Sensor

mahrmediait, 2025-04-16:
Hallo,

I have a toggling toolhead sensor since my last print. Did anyone else have this problem? Any suggestions how to fix?

Best regards
Stefan

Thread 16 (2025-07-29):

Orbiter 2 mount with Orbiter sensor

cray12399, 2025-07-29:
Hello,

I was wondering if there is a version of the orbiter 2 mount that removes the sensor and allows for the use of the orbiter sensor? The mount with the sensor is too high with the filament sensor and bumps into the top of my CPAP ducts.

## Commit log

2024-02-13 Rename VZ Hex+LGX.stl to VZ Hex+LGX Lite.stl
    [VZ Hex+LGX Lite.stl]
2024-03-29 Release V1
    [Bambu Lab.stl, BambuLab.stl, Blade Holder.stl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]
2024-03-29 Create Xol-metrix CAD.step
2024-03-29 Grub screw option in BOM
2024-04-08 cutter arm support rework
    [[a]_cutter_arm.stl]
2024-04-08 added xolpap cuttout
    [extruder_adapter_top_G2SA.stl, extruder_adapter_top_LGX__VZ_Hex.stl, extruder_adapter_top_Orbiter.stl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]
2024-04-08 Updated CAD to reflect changes
2024-07-07 Updet tem ery go woo
    [[a]_cutter_arm.stl, [b]_blade_holder_4.stl, [b]_blade_holder__olfa.stl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]
2024-07-31 Update Xol-metrix CAD.zip
2025-03-17 added TK mounts
